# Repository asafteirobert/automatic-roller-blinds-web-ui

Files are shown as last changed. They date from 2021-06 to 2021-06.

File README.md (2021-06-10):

# Automatic roller blinds web interface
A small NRF24L01 to Wifi gateway. This project is used to control the  [automatic roller blinds motor](https://github.com/asafteirobert/automatic-roller-blinds-motor) project.
It runs a web server which serves a responsive web interface that allows you to control the window blinds and create schedules. It also has an RESTful API which you can use to control the window blinds from most home automation systems.

Built around an ESP32.

The server is self-contained and does not require any connection to cloud IoT services. If you want to connect to something like Blynk App you will need to implement that connectivity yourself. An internet connection is only required to periodically syncronize the time with a public NTP server.

It handles time, time zones, and daylight savings automatically, simply select your timezone.

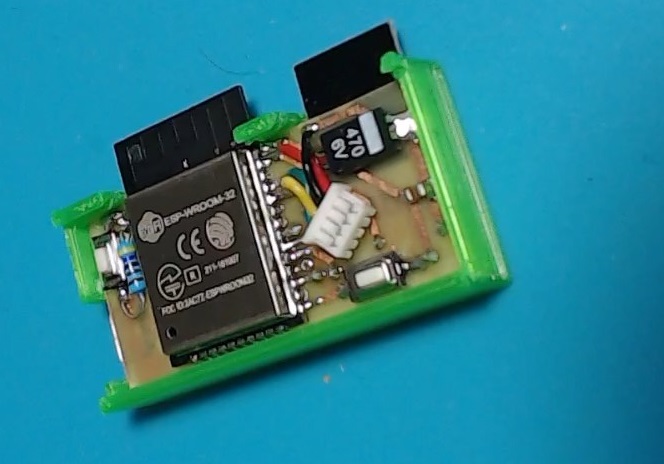
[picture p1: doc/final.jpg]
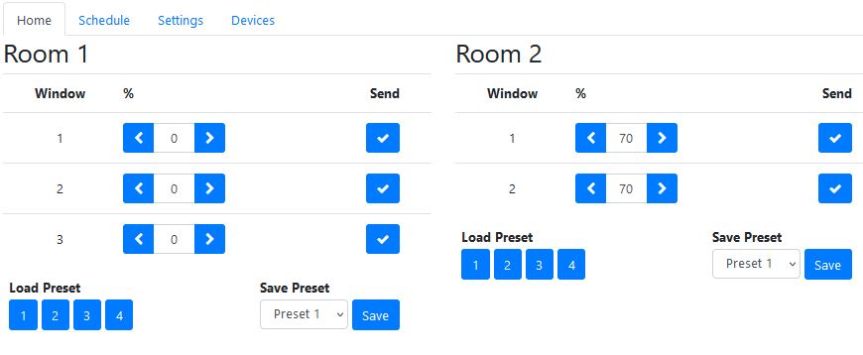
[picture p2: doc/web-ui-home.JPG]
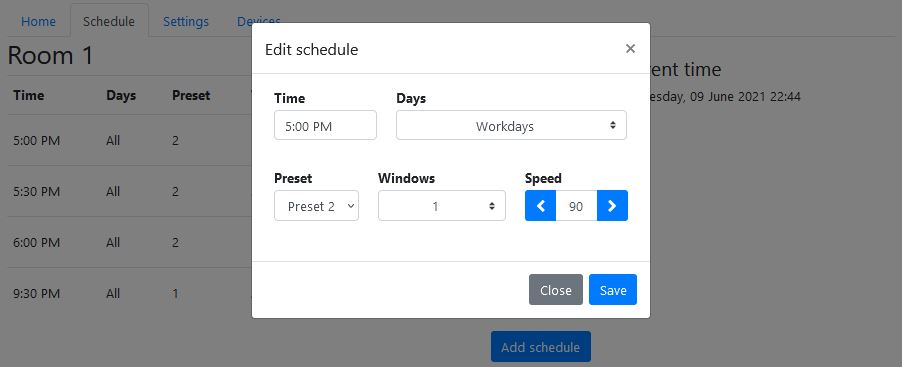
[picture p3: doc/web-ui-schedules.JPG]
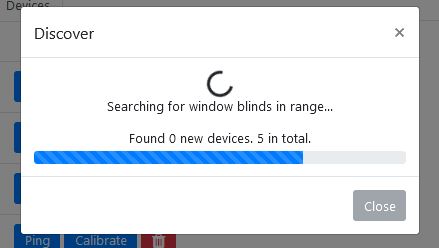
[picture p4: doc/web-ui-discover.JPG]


## How to use it

The gateway is used to is used to control the  [automatic roller blinds motor](https://github.com/asafteirobert/automatic-roller-blinds-motor).

It's powered from 5V connected to the micro USB port, but can be powered by anything between 3.5V and 12V.

First you need to set the WiFi credentials. After connecting the gateway to power, wait a bit then press the BOOT button (GPIO0). This will make the gateway go into configuration mode. It will create an AP called "Window blinds WIFI config Portal". After connecting to it, a captive portal should bring you straight to the configuration page, if not, navigate to 192.168.4.1. Choose one of the access points scanned, enter password, click save. Upon successful connection, the gateway will reboot and start the web server.

Go to any browser in the local network and go to `windowblinds.local` (on Android you will unfortunately need to manually type the IP assigned by your router). Go to the Devices tab and select "Scan for devices". Finally go to the settings page and select your timezone. 

If you didn't do so already, you will need to calibrate the blinds so they know what the maximum and minimum positions are. This can be a bit tedious but should be done carefully as not doing the calibration correctly can damage the blinds. Go to the "Devices" tab and select "Calibrate". Press and hold "Move up" or "Move down" to move the blinds. When the blind is in the correct position, press "Set current position as top/bottom". Now everything is set up and you can use the blinds.

### RESTful API

All aspects of the gateway can be controlled though the RESTful API, but for home automation you should only care about these two GET endpoints:

- `windowblinds.local/setBlinds?roomId=<roomId>&blindNumber=<blindNumber>&targetPercent=<targetPercent>&speed=<speed>`

  - `roomId` and `blindNumber` select the desired blind
  - `targetPercent` sets the percentage to move to (0 - 100)
  - `speed`(optional) sets the speed to move with, in percentage of maximum speed (1 - 100)

  It returns a json with a "message" field which can be
  - `ok` - The command was successful
  - `nrf_send_fail` - The radio command was sent but no radio confirmation was received from the window blinds. The command was likely not executed. The window blind is either offline or out of range.
  - `bad_params` - some parameters are out of range
  - `missing_params` - required parameters are missing

- `windowblinds.local/getStatus?refreshPositions=<refreshPositions>`
  - `refreshPositions`(optional). If `true`, the gateway will first poll all window blinds to check their current target position, otherwise it will simply return the last known position. This is useful if you have other gateways or remotes controlling the window blinds.

  It returns a json containing all the information about the window blinds, schedules, etc.

For the rest of the endpoints, consult the source code.

## Limitations and known issues:
- The range on the NRF24L01 is pretty disappointing, so when controlling the blinds in multiple rooms, it needs to be well positioned for reliable reception. Alternatively, each room or area can each have it's own gateway.
- Android phones still don't support mDNS, so accessing the web interface needs to be done by manually finding and typing the server's local IP.
- Remember, the S in IoT stands for Security. This project is intended to run only in the local network. If you wish to connect to it remotely, you will need to secure and limit access the connection yourself.

## Making your own
All the required files are included in this project. This includes source code, 3D files to be 3D printed, schematic and PCB.
For instructions see [doc/assembly.md](doc/assembly.md).

## Working with the web files

The `data` folder is already prepared, but if you wish to make changes to the web ui, this section explains how to prepare it.

- `www` contains the static web files for the web UI. If you wish to make changes, you will likely need to change `index.html` and `js/scripts.js`
- After making the changes, simply run `tools/prepare data dir.bat` to prepapre the `data` folder. You will need Node.js. If you are not on Windows, you can follow the instructions in the bat file manually.

This step inlines most of the included files into one html and also compresses it. This significanly improves the initial loading time and stability. 

## Project status: Finished, active
All intended functionality is implemented and manually tested. I will try to fix major bugs when they are reported. I will review pull requests, but generally I prefer if you fork the project in order to make your own changes and improvements.

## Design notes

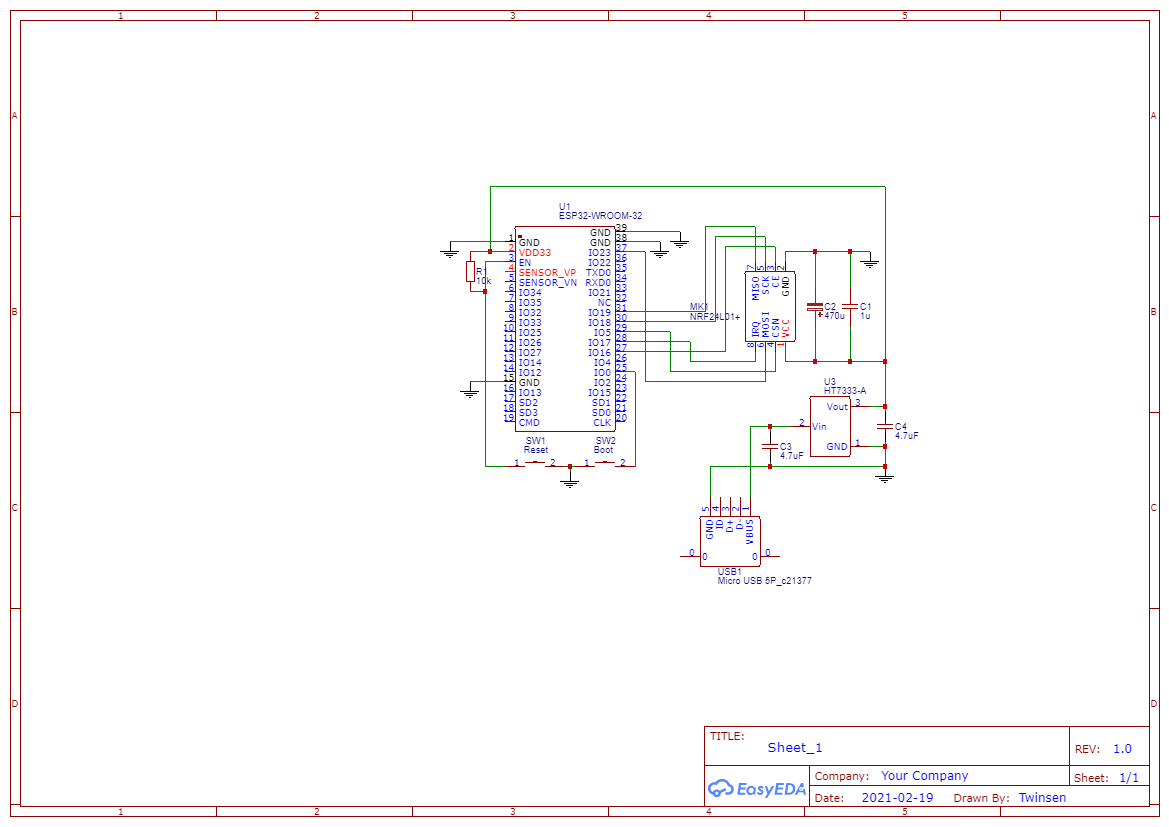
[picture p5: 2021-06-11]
schematic/Schematic_Automatic roller blinds web ui_2021-06-11.png

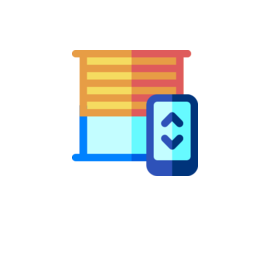
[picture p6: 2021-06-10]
www/mstile-150x150.png

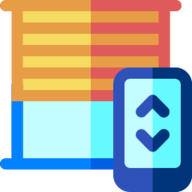
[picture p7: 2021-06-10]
www/android-chrome-192x192.png

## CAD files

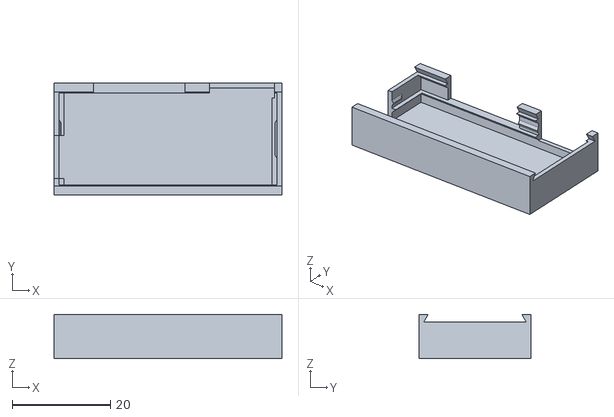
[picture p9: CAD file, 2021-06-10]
3d print/Automatic roller blinds web ui case.stl
46.4 x 22.8 x 9.00

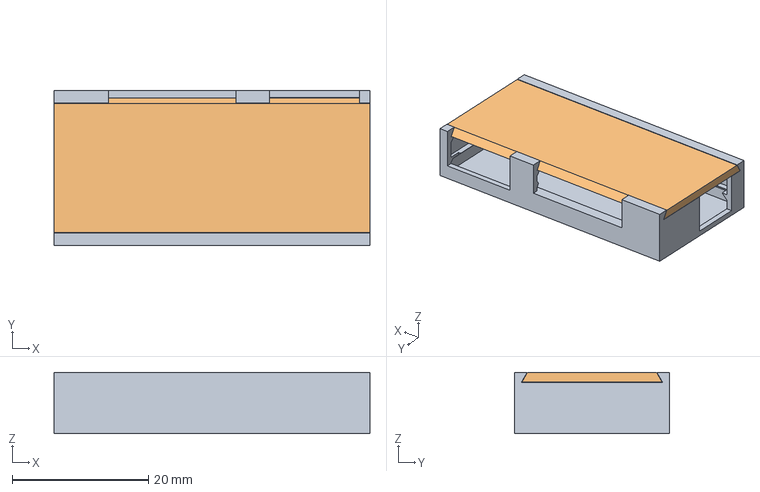
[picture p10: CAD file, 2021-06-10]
3d print/step/Automatic roller blinds web ui case v5.step
46.4 x 22.8 x 9.00 mm

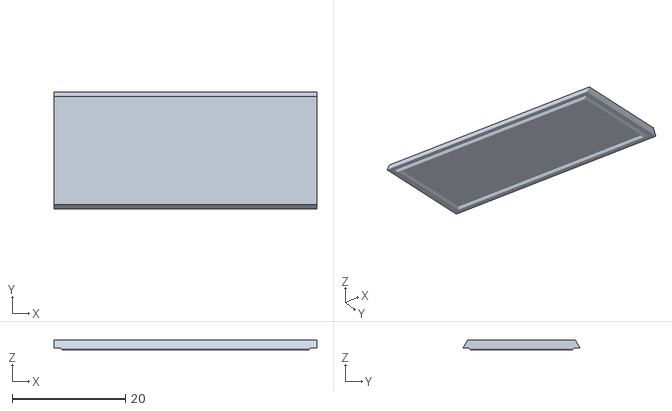
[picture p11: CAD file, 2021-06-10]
3d print/Automatic roller blinds web ui case lid.stl
46.4 x 20.6 x 1.80

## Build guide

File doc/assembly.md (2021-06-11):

# Automatic roller blinds web interface assembly instructions

For this project you will need good soldering skills and some experience with Arduino, ESP32 and Platform IO.

## Materials
- ESP32-WROOM-32 bare module
- 0805 1uf SMD capacitor
- 2x 0805 4.7uf SMD capacitor
- 470uf 6V SMD size C tantalum capacitor
- NRF24L01+	SMD module
- 1206 10k SMD resistor
- 2x 6x3.6x2.5mm pushbuttons
- HT7333 SOT-89 LDO regulator
- Micro USB SMD connector [Something like this](https://lcsc.com/product-detail/USB-Connectors_BOOMELE-Boom-Precision-Elec-C21377_C21377.html) (optional)
- 3D printed case found in `3d print` folder(optional))
- PCB

## The circuit board

If you want to use the 3D printed case, the PCB should be around 0.8mm thick.

You can find the schematic and PCB in the `schematic` folder. It contains an EasyEDA project and Gerber files.

Or simply order the it from this link: https://www.pcbway.com/project/shareproject/Automatic_roller_blinds_web_interface.html

## Steps

1. Solder the components to the PCB. Note that the microusb connector can be difficult to solder currectly. Alternatively, you can solder wires and supply any voltage between 3.5V and 12V.
2. Solder wires to the TX, RX, GND and 3V3 pads and connect them to your USB serial adapter.
3. Put the ESP32 in upload mode by holding both RESET and BOOT, then releasing RESET, then releasing BOOT.
4. Open this project in Platform IO.
5. In Platform IO select `Build Filesystem Image`, then `Upload Filesystem Image`
6. Finally upload the code by selecting `Upload`.
7. Test that it works.
8. Place the board in the 3D printed case (optional).
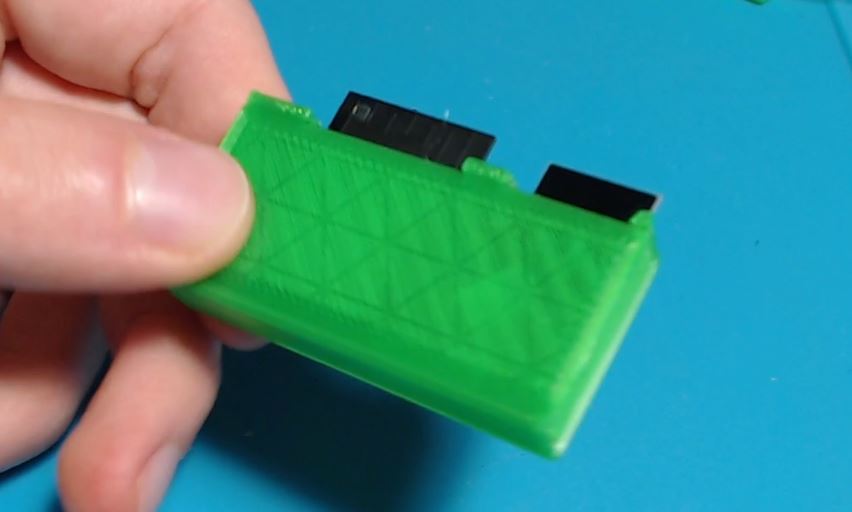
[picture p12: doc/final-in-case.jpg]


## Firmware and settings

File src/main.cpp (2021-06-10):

#include <ESPmDNS.h>
#include <WiFi.h>
#include <ESPAsyncWebServer.h>
#include <ESPAsyncWiFiManager.h>
#include <RF24.h>
#include <AsyncElegantOTA.h>
#include <WiFiUdp.h>
#include <Preferences.h>
#include "SPIFFS.h"
#include "esp32-hal.h"
#include "AsyncJson.h"
#include "ArduinoJson.h"
#include "time.h"

#include "Constants.h"
#include "BlindsData.h"

//#define DEBUG

#ifdef DEBUG
#define DEBUG_PRINT(fmt, ...)  Serial.println(fmt, ##__VA_ARGS__)
#include "printf.h"
#else
#define DEBUG_PRINT(fmt, ...)
#endif

AsyncWebServer server(80);
DNSServer dns;

// RF24 related
RF24 nrfRadio(PIN_NRF_CE, PIN_NRF_CS);
struct SentDataType
{
  int8_t targetPercent;
  uint8_t speed;
};

struct ReturnDataType
{
  uint8_t roomId;
  uint8_t blindId;
  int8_t currentTargetPercent;
};

BlindsData blindsData;

struct DiscoverStatusType
{
  int8_t percent = 0;
  uint8_t devicesCountNew = 0;
  uint8_t devicesCountTotal = 0;
};

volatile DiscoverStatusType discoverStatus;
volatile bool discoverRequested = false;

// ============ NRF functions ============

bool sendPositionUpdate(uint8_t roomId, uint8_t blindId, int8_t targetPercent, uint8_t speed)
{
  uint8_t sendingPipe[5];
  for(uint8_t i = 1; i<5; i++)
    sendingPipe[i] = NRF_PIPE[i];
  sendingPipe[1] = roomId;
  sendingPipe[0] = blindId;
  nrfRadio.openWritingPipe(sendingPipe);

  SentDataType sentData;
  sentData.targetPercent = targetPercent;
  sentData.speed = speed;
  bool sendSuccess = false;
  //DEBUG_PRINT("sending:" + String(roomId)+ " " + String(blindId)+ " " + String(targetPercent)+ " " + String(speed));
  sendSuccess = nrfRadio.write(&sentData, sizeof(sentData));

  ReturnDataType returnedData;
  while (nrfRadio.isAckPayloadAvailable())
  {
    uint8_t len = nrfRadio.getDynamicPayloadSize();
    if (len == sizeof(returnedData))
    {
      nrfRadio.read(&returnedData, sizeof(returnedData));
      //DEBUG_PRINT("received:" + String(returnedData.roomId)+ " " + String(returnedData.blindId)+ " " + String(returnedData.currentTargetPercent));

      if (sendSuccess)
        if (RoomData* room = blindsData.getRoomWithId(roomId))
          if (BlindData* blind = room->getBlindWithId(blindId))
            blind->currentTargetPercent = (targetPercent >= 0) ? targetPercent : returnedData.currentTargetPercent;
    }
    else
    {
      nrfRadio.flush_rx();
      delay(2);
      DEBUG_PRINT("Discarded bad packet <<<");
    }
  }
  if (sendSuccess == true)
  {
    DEBUG_PRINT(F("Transmission success"));
  }
  else
  {
    DEBUG_PRINT(F("Failed transmission"));
  }

  return sendSuccess;
}

void runDiscovery()
{
  discoverStatus.percent = 0;
  discoverStatus.devicesCountTotal = 0;
  discoverStatus.devicesCountNew = 0;
  uint8_t sendingPipe[5];
  for(uint8_t i = 1; i<5; i++)
    sendingPipe[i] = NRF_PIPE[i];

  //loop through all ids and remember who responded
  for (uint8_t currentRoomId = 1; currentRoomId<=BlindsData::MAX_ROOM_COUNT; currentRoomId++)
  {
    for (uint8_t currentBlindId = 1; currentBlindId<=RoomData::MAX_BLIND_COUNT; currentBlindId++)
    {
      sendingPipe[0] = currentBlindId;
      sendingPipe[1] = currentRoomId;
      nrfRadio.openWritingPipe(sendingPipe);

      SentDataType sentData;
      sentData.targetPercent = -1;
      sentData.speed = 100;
      bool sendSuccess = nrfRadio.write(&sentData, sizeof(sentData));

      ReturnDataType returnedData;
      while (nrfRadio.isAckPayloadAvailable())
      {
        uint8_t len = nrfRadio.getDynamicPayloadSize();
        if (len == sizeof(returnedData))
        {
          nrfRadio.read(&returnedData, sizeof(returnedData));
          if (sendSuccess && returnedData.roomId == currentRoomId && returnedData.blindId == currentBlindId)
          {
            discoverStatus.devicesCountTotal++;
            if (!blindsData.containsBlind(currentRoomId, currentBlindId))
            {
              discoverStatus.devicesCountNew++;
              blindsData.addBlind(currentRoomId, currentBlindId, returnedData.currentTargetPercent);
            }
          }
        }
        else
        {
          nrfRadio.flush_rx();
          delay(2);
        }
      }       
      discoverStatus.percent = (((currentRoomId - 1) * RoomData::MAX_BLIND_COUNT + currentBlindId - 1) * 100) / (BlindsData::MAX_ROOM_COUNT * RoomData::MAX_BLIND_COUNT);
      yield();
    }
  }
  blindsData.sort();
  blindsData.saveToSPIFFS();
  discoverStatus.percent = 100;
  discoverRequested = false;
}

void refreshBlindsDataPositions()
{
  for(uint8_t i = 0; i<blindsData.roomsCount; i++)
      for(uint8_t j = 0; j<blindsData.rooms[i].blindsCount; j++)
        {
          //sendPositionUpdate will update stored target if we send -1
          sendPositionUpdate(blindsData.rooms[i].roomId, blindsData.rooms[i].blinds[j].blindId, -1, 100);
        }
}

// ============ Web server functions ============

void notFound(AsyncWebServerRequest *request) 
{
    request->send(404, "text/plain", "Not found");
}

void setupServer()
{
  DEBUG_PRINT("Starting server. IP Address: " + WiFi.localIP().toString());

  server.reset();

  if(!MDNS.begin(HOSTNAME))
  {
    DEBUG_PRINT("Error starting mDNS");
  }

  server.on("/setBlinds", HTTP_GET, [] (AsyncWebServerRequest *request)
  {
    AsyncResponseStream *response = request->beginResponseStream("application/json");
    DynamicJsonDocument result(256);
    uint8_t roomId;
    uint8_t blindNumber;
    int8_t targetPercent;
    uint8_t speed = 100;

    String message;
    if (request->hasParam("roomId") &&
        request->hasParam("blindNumber") &&
        request->hasParam("targetPercent"))
    {
      if (request->hasParam("speed"))
        speed = request->getParam("speed")->value().toInt();
      roomId = request->getParam("roomId")->value().toInt();
      blindNumber = request->getParam("blindNumber")->value().toInt();
      targetPercent = request->getParam("targetPercent")->value().toInt();
      if (targetPercent >= -5 && targetPercent <= 100 && speed >= 1 && speed <= 100)
      {
        if (sendPositionUpdate(roomId, blindNumber, targetPercent, speed))
          message = "ok";
        else
          message = "nrf_send_fail";
      }
      else
        message = "bad_params";
    }
    else 
    {
        message = "missing_params";
    }
    result["message"] = message;
    serializeJson(result, *response);
    request->send(response);
  });

  server.on("/getStatus", HTTP_GET | HTTP_POST, [] (AsyncWebServerRequest *request)
  {
    if (request->hasParam("refreshPositions") && request->getParam("refreshPositions")->value() == "true")
      refreshBlindsDataPositions(); //Ping all the blinds to get their state
    AsyncResponseStream *response = request->beginResponseStream("application/json");
    DynamicJsonDocument json = blindsData.getJson();
    Preferences prefs;
    prefs.begin(PREFERENCES_NAME, true);
    String tzOlson = prefs.getString(PREFERENCES_TZ_OLSON_KEY, String(PREFERENCES_TZ_OLSON_DEFAULT));
    prefs.end();

    json["timezoneOlson"] = tzOlson;

    serializeJson(json, *response);
    request->send(response);
  });

  server.on("/startDiscover", HTTP_GET | HTTP_POST, [] (AsyncWebServerRequest *request)
  {
    AsyncResponseStream *response = request->beginResponseStream("application/json");
    DynamicJsonDocument result(256);
    String message;
    if (discoverRequested)
      message = "already_searching";
    else
    {
      discoverRequested = true;
      discoverStatus.percent = 0;
      discoverStatus.devicesCountNew = 0;
      discoverStatus.devicesCountTotal = 0;
      message = "ok";
    }

    result["message"] = message;
    serializeJson(result, *response);
    request->send(response);
  });

  server.on("/getDiscoveryStatus", HTTP_GET | HTTP_POST, [] (AsyncWebServerRequest *request)
  {
    AsyncResponseStream *response = request->beginResponseStream("application/json");
    DynamicJsonDocument result(512);

    result["percent"] = discoverStatus.percent;
    result["devicesCountNew"] = discoverStatus.devicesCountNew;
    result["devicesCountTotal"] = discoverStatus.devicesCountTotal;
    serializeJson(result, *response);
    request->send(response);
  });

  server.on("/getTimeString", HTTP_GET | HTTP_POST, [] (AsyncWebServerRequest *request)
  {
    AsyncResponseStream *response = request->beginResponseStream("application/json");
    DynamicJsonDocument result(512);

    String message;
    struct tm timeinfo;
    if(getLocalTime(&timeinfo))
    {
      char buf[64];
      if (strftime(buf, 64, "%A, %d %B %Y %H:%M", &timeinfo))
      {
        result["time"] = buf;
        message = "ok";
      }
      else
        message = "print_failed";
    }
    else
      message = "time_not_set";

    result["message"] = message;
    serializeJson(result, *response);
    request->send(response);
  });

  server.on("/forgetBlind", HTTP_GET, [] (AsyncWebServerRequest *request)
  {
    AsyncResponseStream *response = request->beginResponseStream("application/json");
    DynamicJsonDocument result(256);
    uint8_t roomId;
    uint8_t blindNumber;

    String message;
    if (request->hasParam("roomId") &&
        request->hasParam("blindNumber"))
    {
      roomId = request->getParam("roomId")->value().toInt();
      blindNumber = request->getParam("blindNumber")->value().toInt();
      if (blindsData.deleteBlind(roomId, blindNumber))
      {
        message = "ok";
        blindsData.saveToSPIFFS();
      }
      else
        message = "not_found";
    }
    else 
        message = "missing_params";

    result["message"] = message;
    serializeJson(result, *response);
    request->send(response);
  });

  server.on("/deleteSchedule", HTTP_GET, [] (AsyncWebServerRequest *request)
  {
    AsyncResponseStream *response = request->beginResponseStream("application/json");
    DynamicJsonDocument result(256);
    uint8_t roomId;
    uint8_t index;

    String message;
    if (request->hasParam("roomId") &&
        request->hasParam("index"))
    {
      roomId = request->getParam("roomId")->value().toInt();
      index = request->getParam("index")->value().toInt();
      if (blindsData.deleteSchedule(roomId, index))
      {
        message = "ok";
        blindsData.saveToSPIFFS();
      }
      else
        message = "not_found";
    }
    else 
        message = "missing_params";

    result["message"] = message;
    serializeJson(result, *response);
    request->send(response);
  });

  server.on("/addSchedule", HTTP_GET, [] (AsyncWebServerRequest *request)
  {
    AsyncResponseStream *response = request->beginResponseStream("application/json");
    DynamicJsonDocument result(256);
    uint8_t roomId;
    ScheduleData newSchedule;

    String message;
    if (request->hasParam("roomId") &&
        request->hasParam("timeH") &&
        request->hasParam("timeM") &&
        request->hasParam("days") &&
        request->hasParam("preset") &&
        request->hasParam("windows") &&
        request->hasParam("speed"))
    {
      roomId = request->getParam("roomId")->value().toInt();
      newSchedule.timeH = request->getParam("timeH")->value().toInt();
      newSchedule.timeM = request->getParam("timeM")->value().toInt();
      newSchedule.days = request->getParam("days")->value().toInt();
      newSchedule.preset = request->getParam("preset")->value().toInt();
      newSchedule.windows = request->getParam("windows")->value().toInt();
      newSchedule.speed = request->getParam("speed")->value().toInt();
      if (newSchedule.isValid())
      {
        if (blindsData.addSchedule(roomId, newSchedule))
        {
          message = "ok";
          blindsData.saveToSPIFFS();
        }
        else
          message = "add_failed";
      }
      else
        message = "bad_params";
    }
    else 
      message = "missing_params";

    result["message"] = message;
    serializeJson(result, *response);
    request->send(response);
  });

  server.on("/editSchedule", HTTP_GET, [] (AsyncWebServerRequest *request)
  {
    AsyncResponseStream *response = request->beginResponseStream("application/json");
    DynamicJsonDocument result(256);
    uint8_t index;
    uint8_t roomId;
    ScheduleData newSchedule;

    String message;
    if (request->hasParam("index") &&
        request->hasParam("roomId") &&
        request->hasParam("timeH") &&
        request->hasParam("timeM") &&
        request->hasParam("days") &&
        request->hasParam("preset") &&
        request->hasParam("windows") &&
        request->hasParam("speed"))
    {
      index = request->getParam("index")->value().toInt();
      roomId = request->getParam("roomId")->value().toInt();
      newSchedule.timeH = request->getParam("timeH")->value().toInt();
      newSchedule.timeM = request->getParam("timeM")->value().toInt();
      newSchedule.days = request->getParam("days")->value().toInt();
      newSchedule.preset = request->getParam("preset")->value().toInt();
      newSchedule.windows = request->getParam("windows")->value().toInt();
      newSchedule.speed = request->getParam("speed")->value().toInt();
      if (newSchedule.isValid())
      {
        if (blindsData.deleteSchedule(roomId, index))
        {
          if (blindsData.addSchedule(roomId, newSchedule))
          {
            message = "ok";
            blindsData.saveToSPIFFS();
          }
          else
            message = "add_failed";
        }
        else
          message = "not_found";
      }
      else
        message = "bad_params";
    }
    else 
      message = "missing_params";

    result["message"] = message;
    serializeJson(result, *response);
    request->send(response);
  });

  server.on("/setTimezone", HTTP_GET, [] (AsyncWebServerRequest *request)
  {
    AsyncResponseStream *response = request->beginResponseStream("application/json");
    DynamicJsonDocument result(256);

    String message;
    if (request->hasParam("timezonePosix") &&
        request->hasParam("timezoneOlson"))
    {
      String timezonePosix = request->getParam("timezonePosix")->value();
      String timezoneOlson = request->getParam("timezoneOlson")->value();
      if (timezonePosix.length() > 0 && timezonePosix.length() <= 50 && timezoneOlson.length() > 0 && timezoneOlson.length() <= 100)
      {
        Preferences prefs;
        prefs.begin(PREFERENCES_NAME, false);
        if (prefs.putString(PREFERENCES_TZ_OLSON_KEY, timezoneOlson) &&
            prefs.putString(PREFERENCES_TZ_POSIX_KEY, timezonePosix))
            {
              setenv("TZ", timezonePosix.c_str(), 1);
              tzset();
              message = "ok";
            }
        else
          message = "prefs_put_fail";
        prefs.end();
      }
      else
        message = "bad_params";
    }
    else 
      message = "missing_params";

    result["message"] = message;
    serializeJson(result, *response);
    request->send(response);
  });

  AsyncCallbackJsonWebHandler *updatePresetHandler = new AsyncCallbackJsonWebHandler("/updatePreset", [](AsyncWebServerRequest *request, JsonVariant &json) {
    StaticJsonDocument<256> body = json.as<JsonObject>();
    AsyncResponseStream *response = request->beginResponseStream("application/json");
    DynamicJsonDocument result(256);
    String message;

    if (body.containsKey("roomId") &&
        body.containsKey("presetIndex") &&
        body.containsKey("newPreset"))
    {
      if (body["newPreset"].is<JsonArray>() && body["roomId"].is<int>() && body["presetIndex"].is<int>())
      {
        uint8_t roomId = body["roomId"].as<int>();
        uint8_t presetIndex = body["presetIndex"].as<int>();
        if (RoomData* room = blindsData.getRoomWithId(roomId))
        {
          if (body["newPreset"].as<JsonArray>().size() == room->blindsCount && presetIndex < RoomData::PRESET_COUNT)
          {
            bool ok = true;
            for (JsonVariant value : body["newPreset"].as<JsonArray>())
              if (!(value.is<int>() && value.as<int>() >= 0 && value.as<int>() <= 100))
              {
                ok = false;
                break;
              }
            if (ok)
            {
              uint8_t index = 0;
              for (JsonVariant value : body["newPreset"].as<JsonArray>())
                room->blindsPresets[presetIndex][index++] = value.as<int>();
              message = "ok";
            }
            else
              message = "bad_params";
          }
          else
            message = "bad_params";
        }
        else
          message = "not_found";
      }
      else
        message = "bad_params";
    }
    else 
      message = "missing_params";

    result["message"] = message;
    serializeJson(result, *response);
    request->send(response);
  });
  server.addHandler(updatePresetHandler);

  server.serveStatic("/", SPIFFS, "/www/")
        .setDefaultFile("index.html");
        //.setCacheControl("max-age=6000");


  AsyncElegantOTA.begin(&server);

  server.onNotFound(notFound);

  server.begin();
}

// ============ Other ============

#ifdef DEBUG
void timeSyncNotificationCallback(struct timeval *tv)
{
    DEBUG_PRINT("Time synced with NTP");
}
#endif
// ============ Schedule ============

unsigned long lastScheduleUpdate = 0;
unsigned long lastSaveOnReschedule = 0;

void checkSchedules()
{
  if (!(WiFi.isConnected() && WiFi.getMode() == WIFI_STA))
    return;
  time_t timeNow;
  time(&timeNow);
  for(uint8_t roomIndex = 0; roomIndex < blindsData.roomsCount; roomIndex++)
    for (uint8_t scheduleIndex = 0; scheduleIndex < blindsData.rooms[roomIndex].scheduleCount; scheduleIndex++)
    {
      RoomData& currentRoom = blindsData.rooms[roomIndex];
      ScheduleData& currentSchedule = currentRoom.schedules[scheduleIndex];
      if (currentSchedule.nextTrigger > 0 && 
          currentSchedule.nextTrigger <= timeNow)
      {
        //if the event was supposed to happen some time ago(e.g. device was offline), don't execute the action, just reschedule it
        bool tooLate = (timeNow - currentSchedule.nextTrigger > 15*60);

        if (!tooLate)
        {
          DEBUG_PRINT("Scheduled event triggered");
          for (uint8_t blindIndex = 0; blindIndex < currentRoom.blindsCount; blindIndex++)
            if (currentSchedule.windows & (1<<(currentRoom.blinds[blindIndex].blindId-1)))
            {
              sendPositionUpdate(currentRoom.roomId,
                                 currentRoom.blinds[blindIndex].blindId,
                                 currentRoom.blindsPresets[currentSchedule.preset-1][blindIndex],
                                 currentSchedule.speed);
              yield();
            }
        }

        time_t nextTrigger;
        struct tm nextTriggerLocalTime;
        //convert trigger epoch time into local timezone time
        localtime_r(&currentSchedule.nextTrigger, &nextTriggerLocalTime);
        
        //hour and minute should stay the same regardless of dst changes
        assert(nextTriggerLocalTime.tm_hour == currentSchedule.timeH);
        assert(nextTriggerLocalTime.tm_min == currentSchedule.timeM);

        //move to next day until the trigger satisfies all conditions
        do
        {
          nextTriggerLocalTime.tm_mday++;
          nextTriggerLocalTime.tm_isdst = -1; //we dont know, mktime will set it
          nextTrigger = mktime(&nextTriggerLocalTime);
        } while (!(nextTrigger > timeNow && currentSchedule.isCorrectTrigger(nextTriggerLocalTime)));

        DEBUG_PRINT(&nextTriggerLocalTime, "Rescheduling event for %A, %B %d %Y %H:%M:%S");
        currentSchedule.nextTrigger = nextTrigger;

        //save blindsData every 24h when events are resheduled
        unsigned long currentMillis = millis();
        if (currentMillis - lastScheduleUpdate > 24*60*60*1000)
        {
          blindsData.saveToSPIFFS();
          DEBUG_PRINT("Saving blindsData");
        }
      }
    }
}
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
void loop()
{
  unsigned long currentMillis = millis();
  // is configuration portal requested?
  if ( digitalRead(PIN_TRIGGER_CONFIG_PORTAL) == LOW )
  {
    MDNS.end();
    DEBUG_PRINT("Trigger pressed, starting WifiManager");
    AsyncWiFiManager wifiManager(&server,&dns);
    wifiManager.setTryConnectDuringConfigPortal(false);
    wifiManager.setTimeout(600);

    if (!wifiManager.startConfigPortal("Window blinds WIFI config Portal"))
    {
      DEBUG_PRINT("wifiManager failed to connect to a network");
    }
    else
    {
      setupServer();
    }
  }

  if (discoverRequested)
  {
    runDiscovery();
  }

  if (currentMillis - lastScheduleUpdate > 5000)
  {
    lastScheduleUpdate = currentMillis;
    struct tm timeinfo;
    if(!getLocalTime(&timeinfo))
    {
      DEBUG_PRINT("Failed to obtain local time");
    }
    else
      Serial.println(&timeinfo, "%A, %B %d %Y %H:%M:%S");
    checkSchedules();
  }

  yield();
}

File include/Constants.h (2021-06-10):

#ifndef _CONSTANTS_h
#define _CONSTANTS_h
#include "arduino.h"

// ======= Config =======
const static char* HOSTNAME = "windowblinds";

// ======= Pin defination =======
const uint8_t PIN_NRF_CE = 16;
const uint8_t PIN_NRF_CS = 5;
const uint8_t PIN_TRIGGER_CONFIG_PORTAL = 0;

// ======= NRF =======
const static uint8_t NRF_PIPE[5] = {0x01, 0x01, 0x0e, 0xf1, 0xbf};//first byte is blind id, second byte is room id
const static uint8_t NRF_CHANNEL = 103;

// Other
const static char* PREFERENCES_NAME = "windowblinds";
const static char* PREFERENCES_TZ_POSIX_KEY = "tz_posix";
const static char* PREFERENCES_TZ_OLSON_KEY = "tz_olson";
const static char* PREFERENCES_TZ_POSIX_DEFAULT = "CET-1CEST,M3.5.0,M10.5.0/3";
const static char* PREFERENCES_TZ_OLSON_DEFAULT = "CET";

#endif

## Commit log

2021-06-10 Initial project commit
    [Automatic roller blinds web ui case lid.stl, Automatic roller blinds web ui case v5.step, Automatic roller blinds web ui case.stl]
2021-06-11 Added PCB order link
2021-06-11 Added schematic image
